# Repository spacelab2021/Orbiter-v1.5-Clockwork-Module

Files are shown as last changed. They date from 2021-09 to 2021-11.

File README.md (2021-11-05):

# Orbiter Clockwork Module
This Clockwork module allows the use of the Orbiter v1.5 Extruder in the Voron Afterburner.

## Features
One of the main issues I observed when using the orbiter was a lack of a quick filament release in additional to a lack of a suitable clockwork adapter that would swap an orbiter directly into the Afterburner ecosystem. Many of the issues observed were addressed with this Clockwork Module. This version provides a chain anchor for the Voron 2.4 and the Switchwire, a Cable Cover, and a quick filament release lever.

## Bill of Materials (BOM)

| Quantity | Name | Type |
|---|---|---|
| 1 | Orbiter v1.5 Extruder [Orbiter Thingiverse link](https://www.thingiverse.com/thing:4725897) | Hardware  |  
| 9 | M3 Heat Set Inserts [McMaster Link](https://www.mcmaster.com/94180A331) | Hardware  |  
| |94180A331 or suitable inserts (Thread Pitch 0.5, Installed Length 3.8mm, Diameter ~5mm) | | 
| 1 | M3x8mm SHCS | Hardware  |  
| 2 | M3x10mm SHCS | Hardware  |  
| 1 | M3x12 SHCS | Hardware  | 
| 2 | M3x20 SHCS | Hardware  |
| 1 | PTFE 50mm (Dragon) | Hardware  |
| 1 | Clockwork Adaptor - Front | Printable |
| 1 | Clockwork Adaptor - Back | Printable |
| 1 | Cable/Connector Cover | Printable |
| 1 | Filament Quick Release | Printable |
| 1 | Chain Anchor (Version for Voron 1.8/Trident/2.4 and Switchwire) | Printable |

## Assembly Guide
* [Orbiter Clockwork Assembly Guide](./docs/Orbiter_Clockwork_Manual.pdf)

## Orbiter Clockwork Module Images
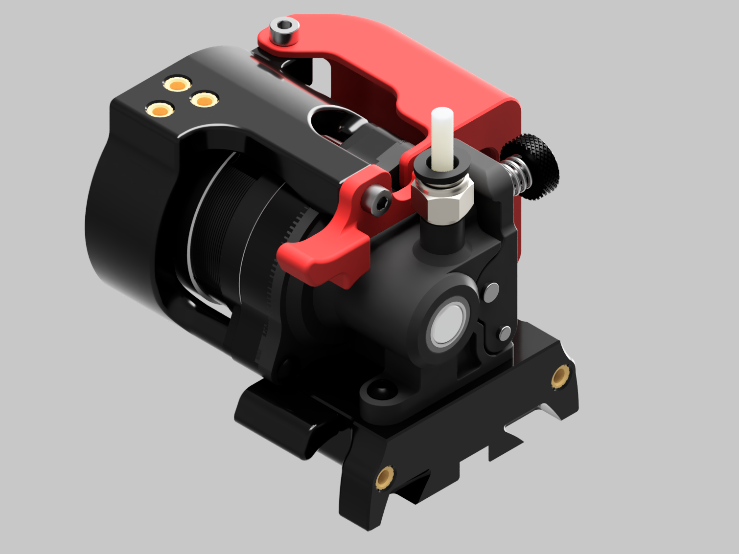
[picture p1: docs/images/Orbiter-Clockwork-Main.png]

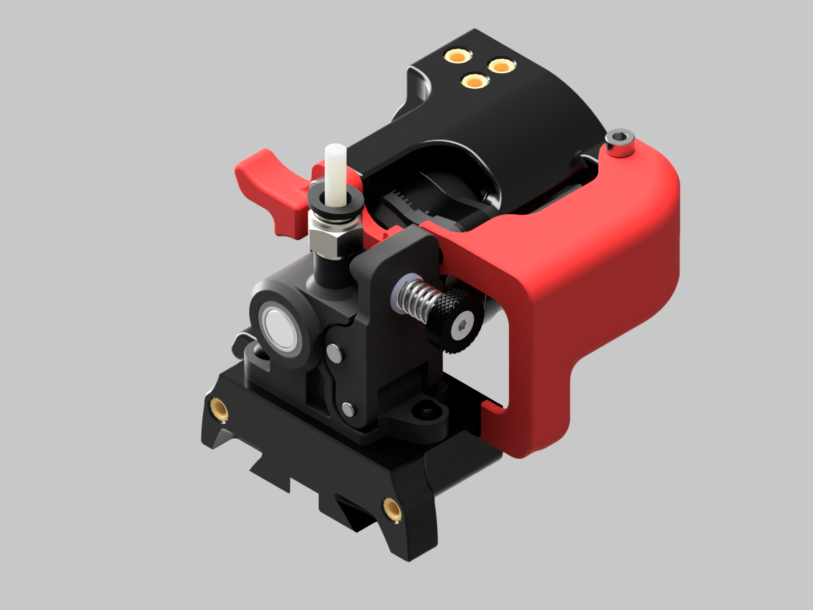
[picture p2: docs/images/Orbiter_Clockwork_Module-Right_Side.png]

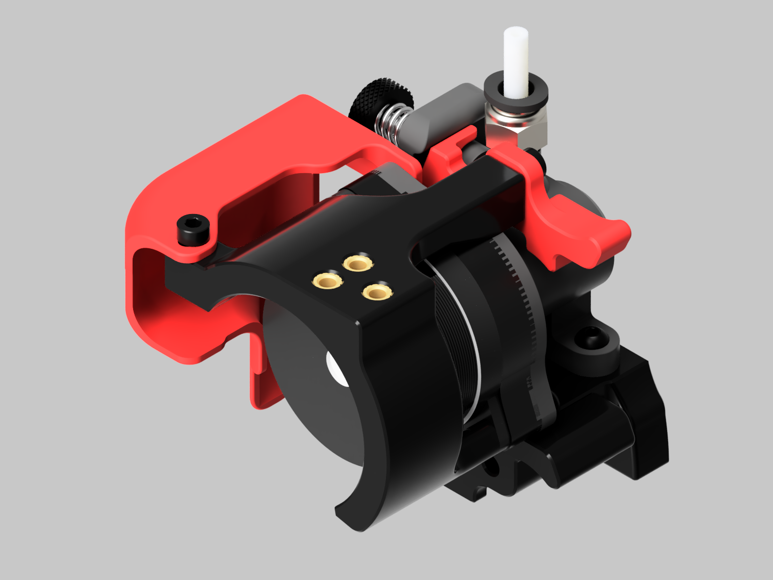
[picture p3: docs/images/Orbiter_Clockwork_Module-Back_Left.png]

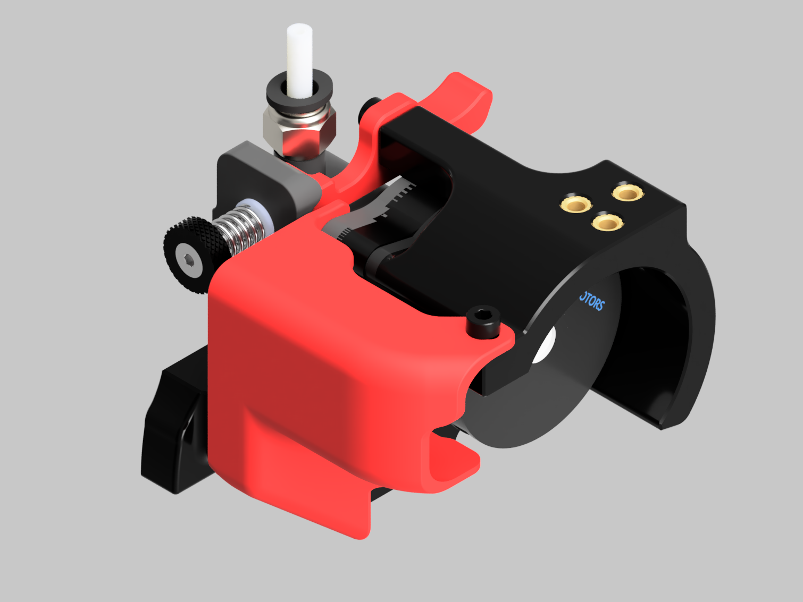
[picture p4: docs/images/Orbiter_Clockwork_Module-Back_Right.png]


## Release History
* Version 1.0 
   * Orbiter Clockwork Adaptor has been verified to fit and function on a Voron 2.4 and a Switchwire. Additional testing may be required to fix any minor or major issues that are identified in the future. If you observed any issues, please create an issue so it can be tracked.

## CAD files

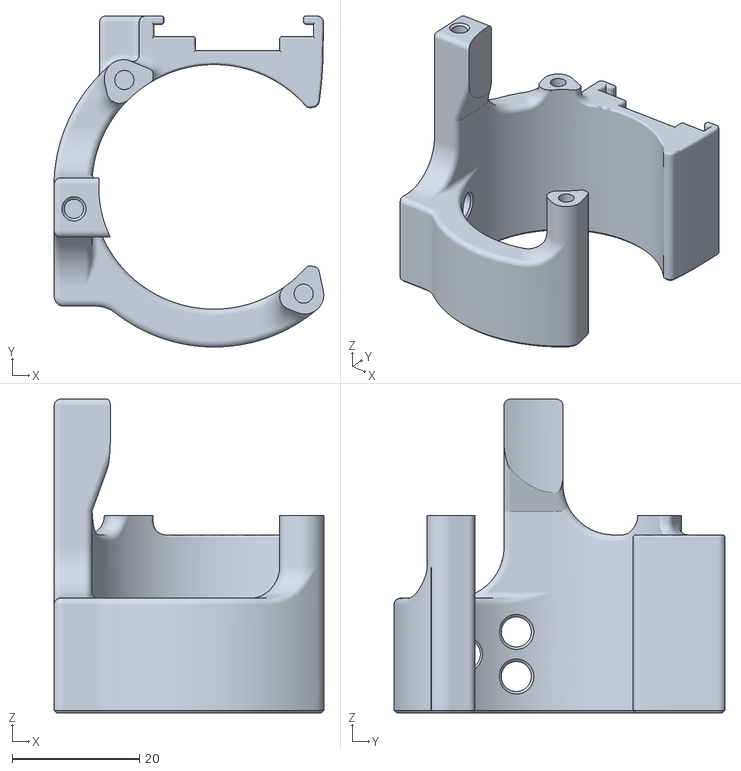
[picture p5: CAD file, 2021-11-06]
stl/Chain_Anchor-PCB_Mount-Generic-2.4.stl
42.3 x 52.0 x 49.2

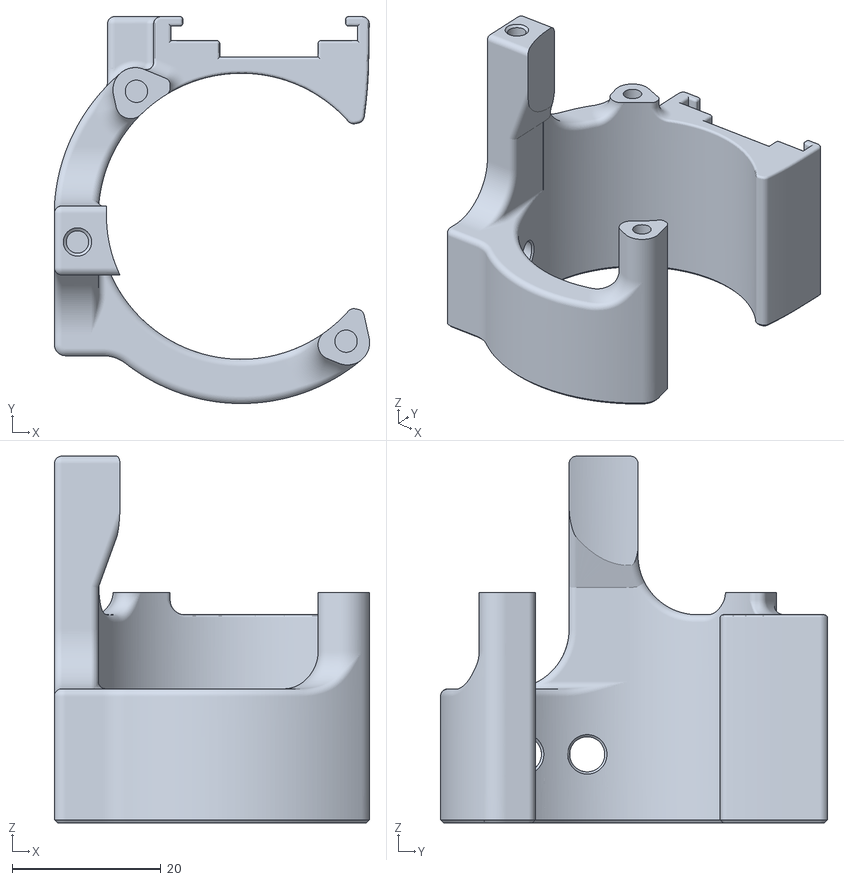
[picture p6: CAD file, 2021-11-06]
stl/Chain_Anchor-PCB_Mount-Igus-2.4.stl
42.3 x 52.0 x 49.2

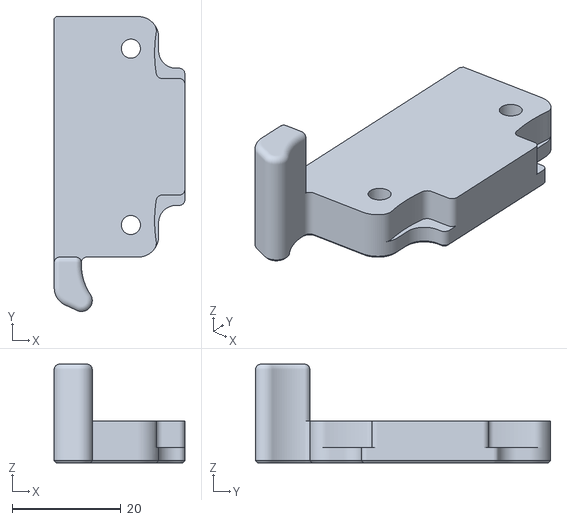
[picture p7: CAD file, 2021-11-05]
stl/Clockwork_Adaptor_Back.stl
24.0 x 54.2 x 18.1

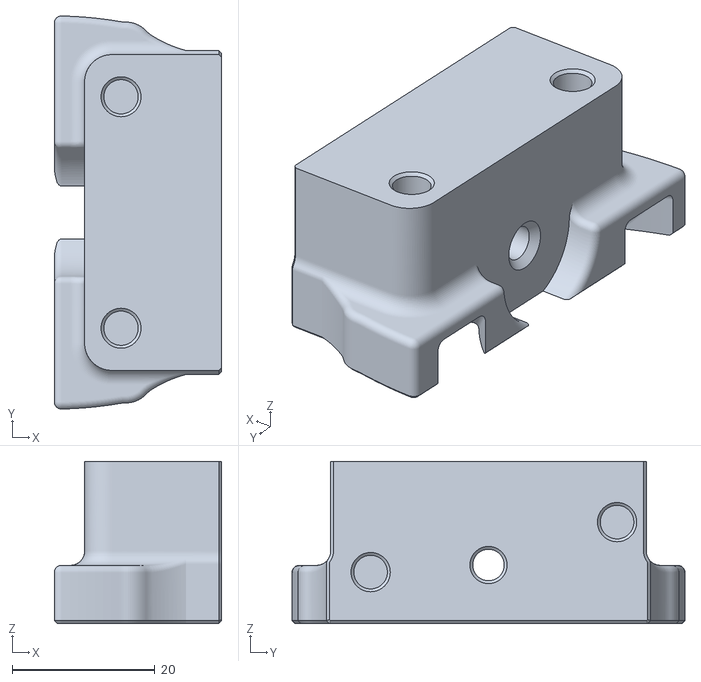
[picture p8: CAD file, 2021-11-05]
stl/Clockwork_Adaptor_Front.stl
23.4 x 55.0 x 22.7

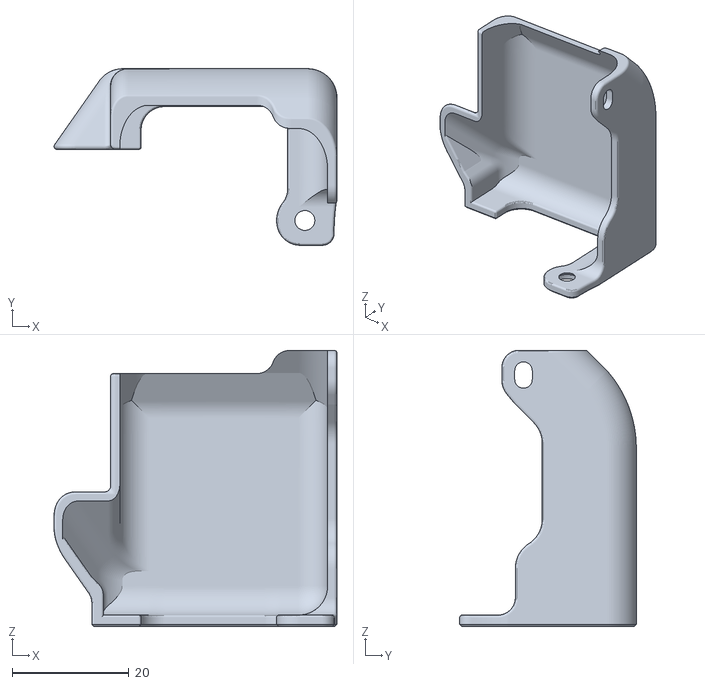
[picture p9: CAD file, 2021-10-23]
stl/[a]_PCB_Connector_Cover.stl
48.5 x 30.3 x 47.4

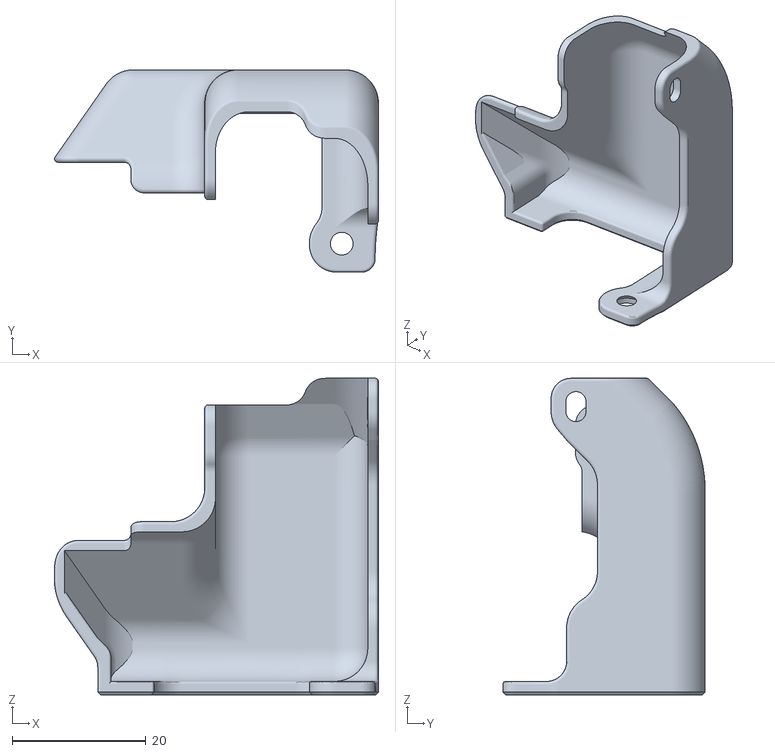
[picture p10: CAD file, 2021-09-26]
stl/[a]_Connector_Cover.stl
48.5 x 30.3 x 47.4

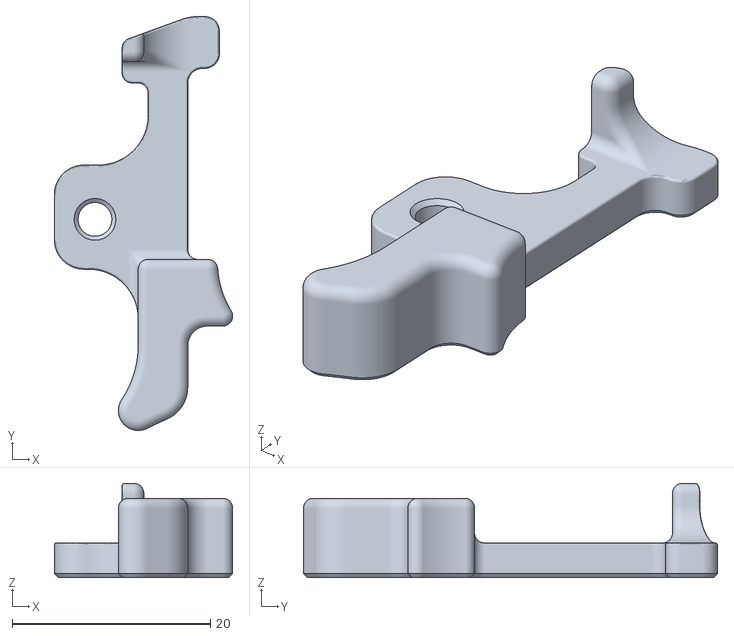
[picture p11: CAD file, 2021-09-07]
stl/[a]_Filament_release_lever.stl
18.0 x 41.7 x 9.50

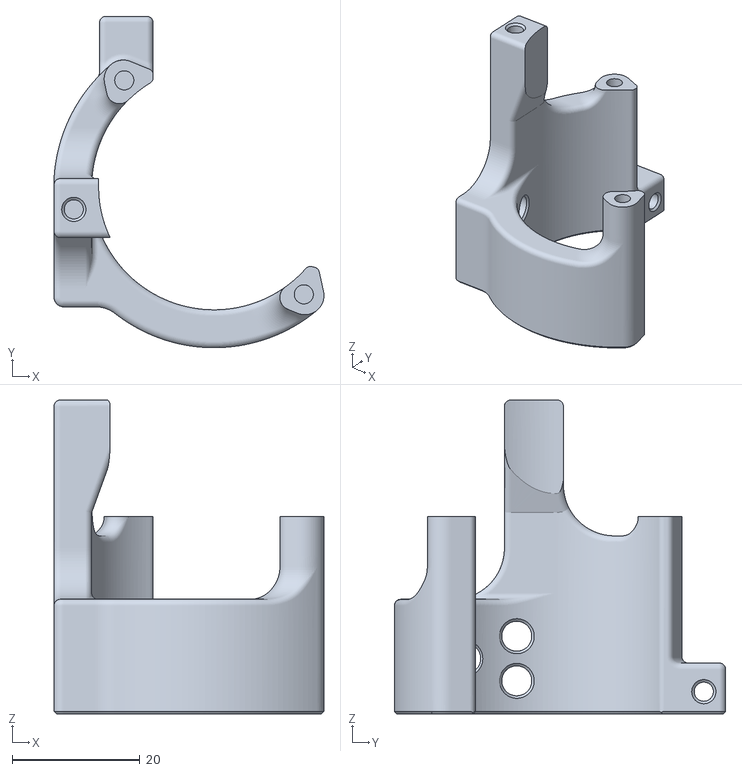
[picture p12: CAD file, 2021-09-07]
stl/Chain_Anchor-Voron_2.4.stl
42.3 x 52.0 x 49.2

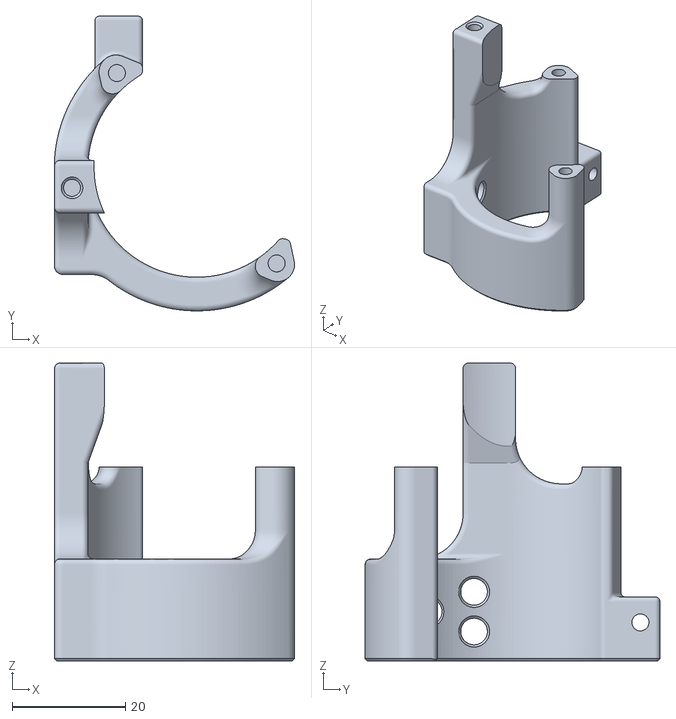
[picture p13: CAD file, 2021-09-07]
stl/Chain_Anchor_SwitchWire.stl
42.3 x 52.0 x 52.5

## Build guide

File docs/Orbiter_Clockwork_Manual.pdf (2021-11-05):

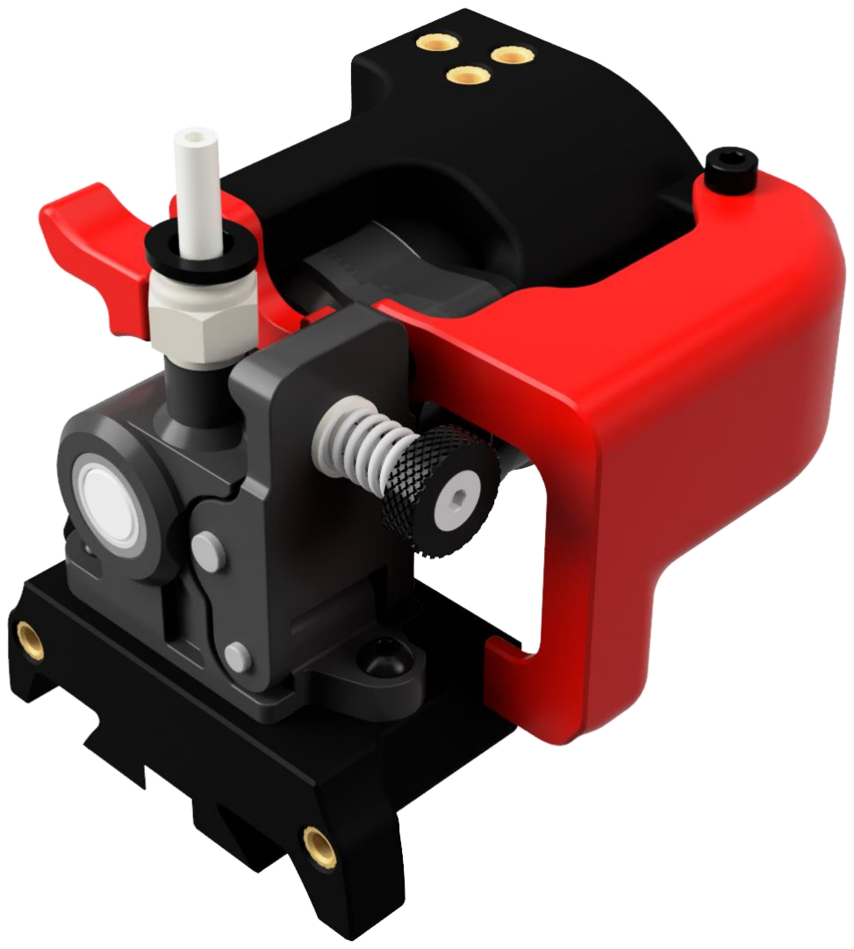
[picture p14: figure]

# ORBITER CLOCKWORK ASSEMBLY MANUAL

## MANUAL VERSION 1.0.3

Orbiter Clockwork Assembly Manual | 2

## HARDWARE

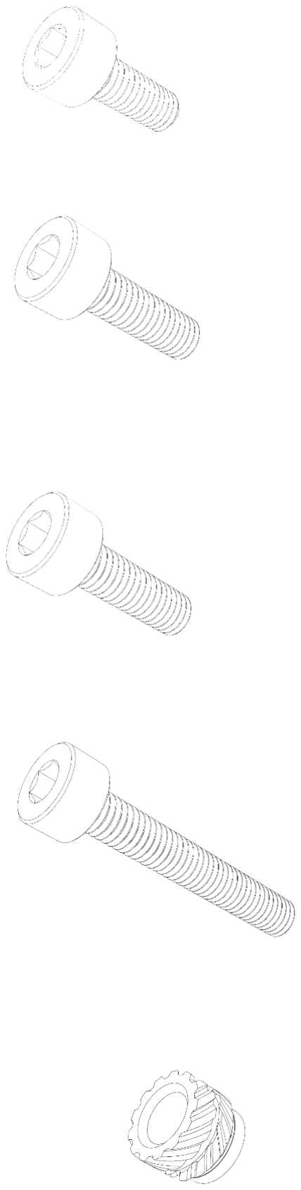
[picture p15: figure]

### SOCKET HEAD CAP SCREW (SHCS)

Metricfastenerwithacylindricalheadand hex drive.

### M3x8 Quantity 1

### SOCKET HEAD CAP SCREW (SHCS)

Metric fastener with a cylindrical head and hex drive.

### M3x10 Quantity 2

### SOCKET HEAD CAP SCREW (SHCS)

Metric fastener with a cylindrical head and hex drive.

### M3x12 Quantity 1

### SOCKET HEAD CAP SCREW (SHCS)

Metric fastener with a cylindrical head and hex drive.

### M3x20 Quantity 2

### TAPERED HEAT-SET INSERTS FOR PLASTIC

### The tapered shape makes it easier to guide these inserts into a hole during installation. Use a drill bit to create a straight hole, then taper the top half. Heat inserts with a

soldering tip so that they melt the plastic when installed.

### As the plastic cools, it solidifies around the knurls and ridges on the insert for excellent resistance to both torque

and pull-out.

### M3 Brass Heat-Set Insert Quantity: 9

### PTFE Tube

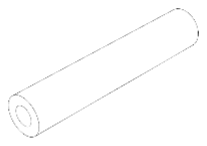
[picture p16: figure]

### The PTFE tube is used between the Orbiter extruder and the Toolhead. Specific hot end lengths are listed below:

### Phaetus Dragon Hotend PTFE Tube Length 50mm

### E3D V6 Hot end PTFE Tube Length ??mm (Not Tested Yet)

### Slice Engineering Mosquito Hot end PTFE Tube Length ??mm (Not Tested Yet)

## PRINTED PARTS

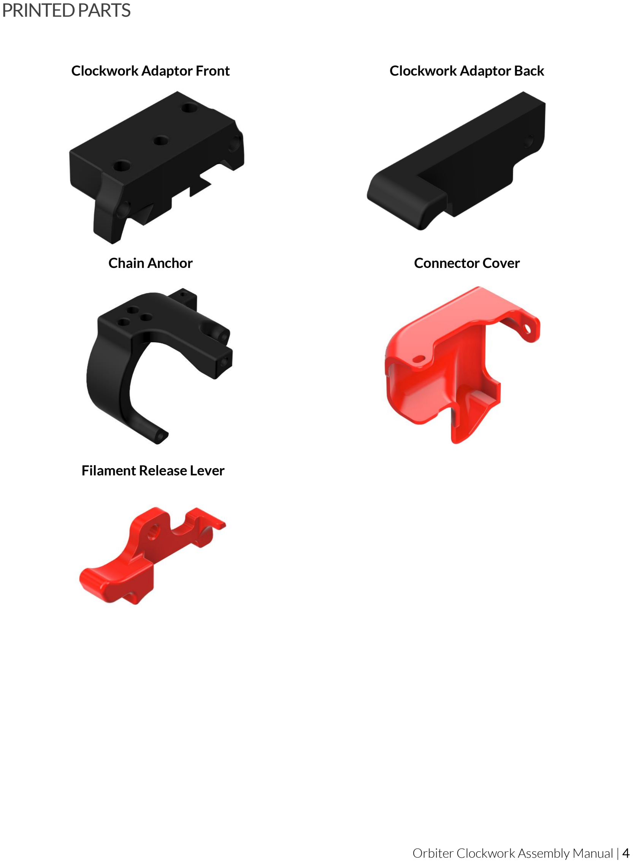
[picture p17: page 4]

Clockwork Adaptor Front | Clockwork Adaptor Back

### Chain Anchor

### Connector Cover

### Filament Release Lever

## ASSEMBLYGUIDE

# Assembly A. Heat-Set Inserts

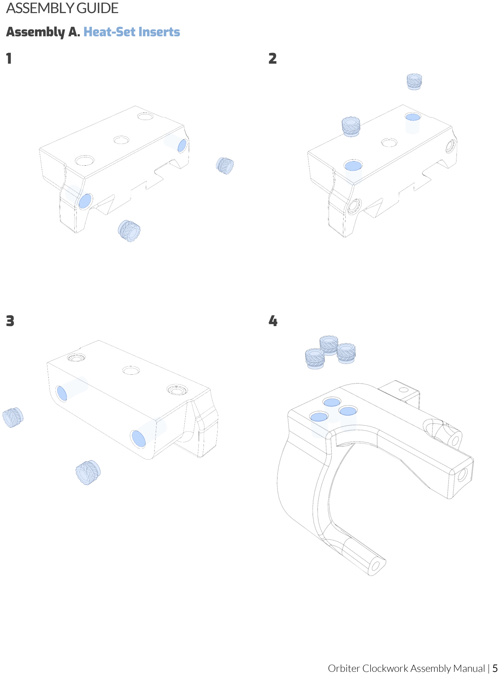
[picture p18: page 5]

1 2

3 4

# Assembly B. Orbiter Clockwork Adapter

5

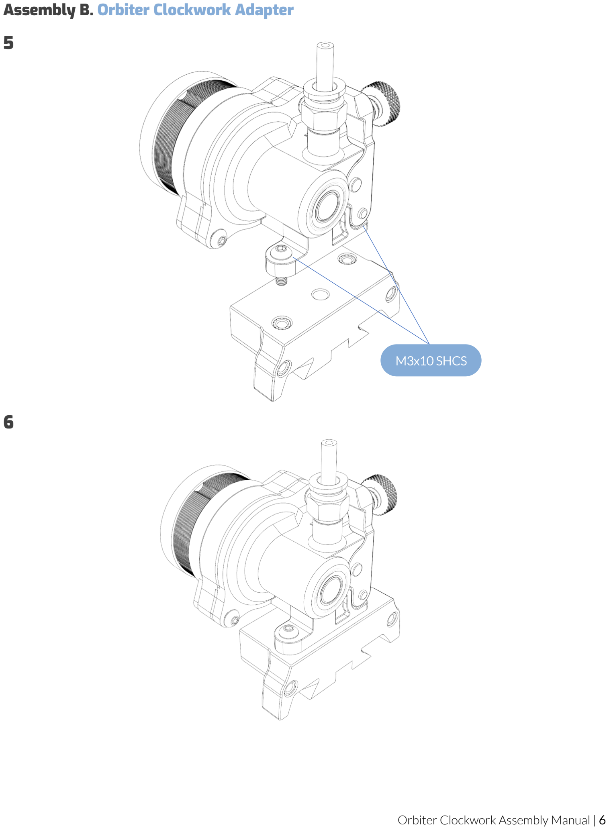
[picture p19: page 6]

6

M3x10 SHCS

# Assembly C. Connecter Cover and Chain Anchor

7 8

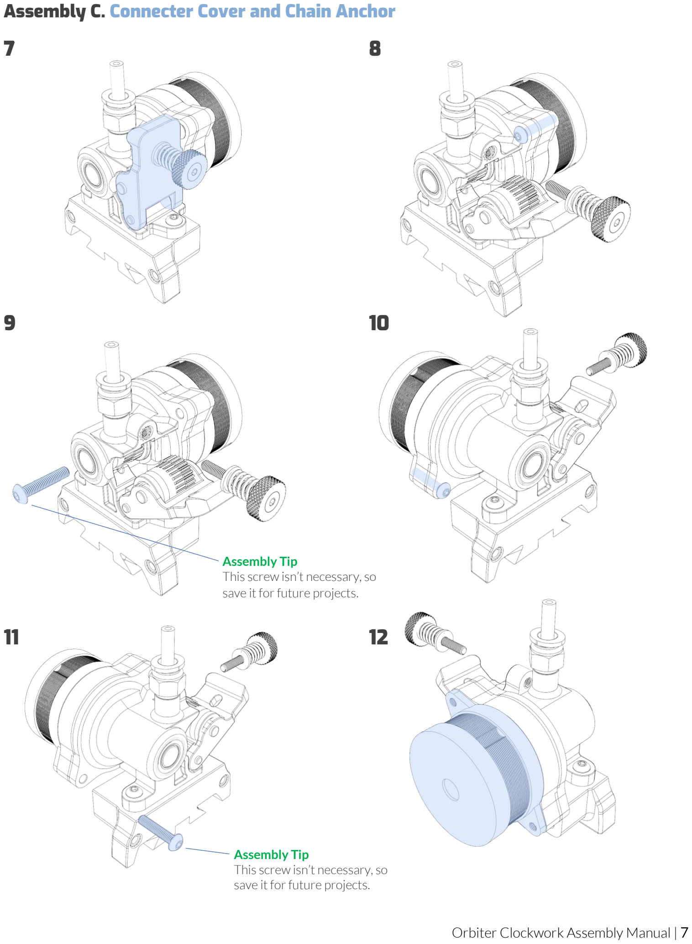
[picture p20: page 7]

9 10

11 12

Assembly Tip
This screw isn’t necessary, so save it for future projects.

Assembly Tip
This screw isn’t necessary, so save it for future projects.

13 14

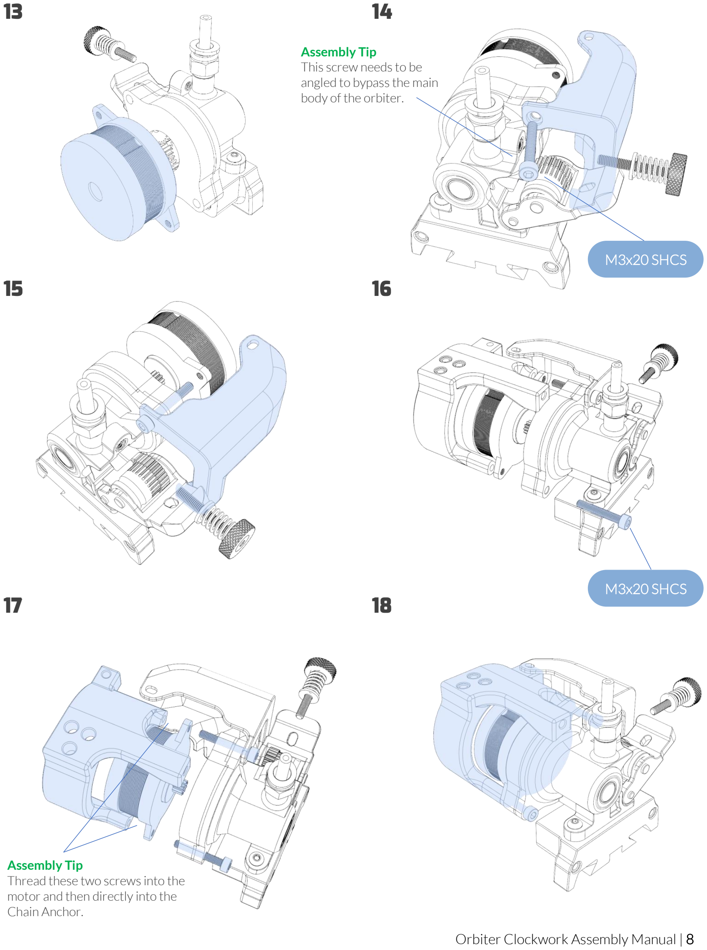
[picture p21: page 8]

15 16

17 18

M3x20 SHCS

M3x20 SHCS

Assembly Tip
Thread these two screws into the motor and then directly into the Chain Anchor.

Assembly Tip
This screw needs to be
angled to bypass the main
body of the orbiter.

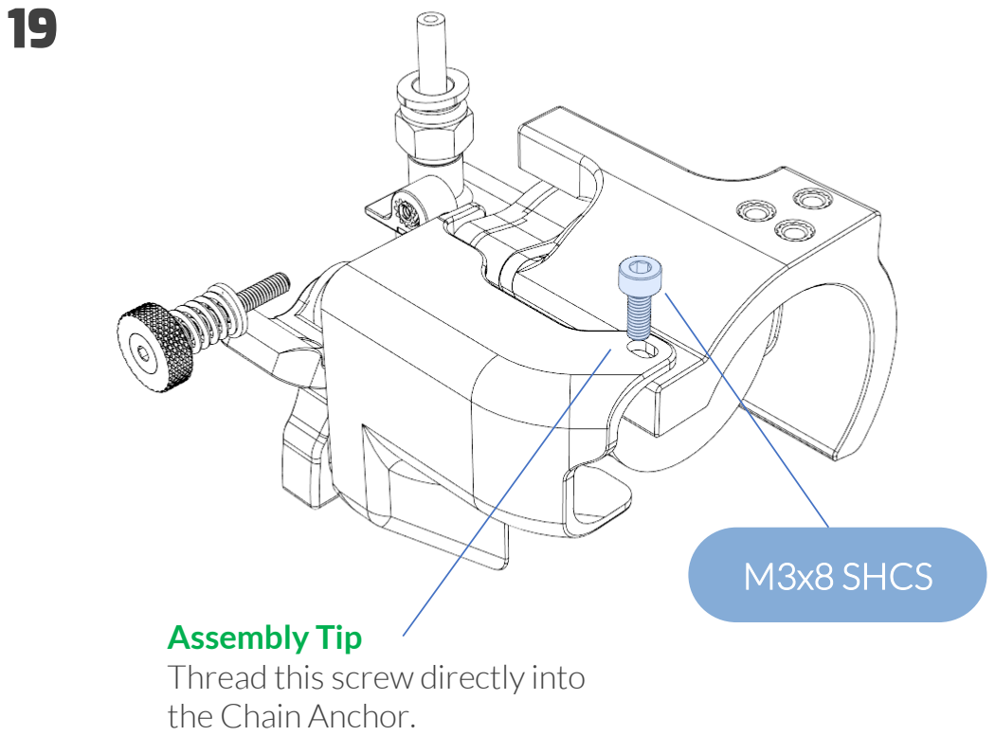
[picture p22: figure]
M3x8 SHCS; Assembly Tip Thread this screw directly into the Chain Anchor.

# Assembly D. Filament Quick Release Lever

20 21

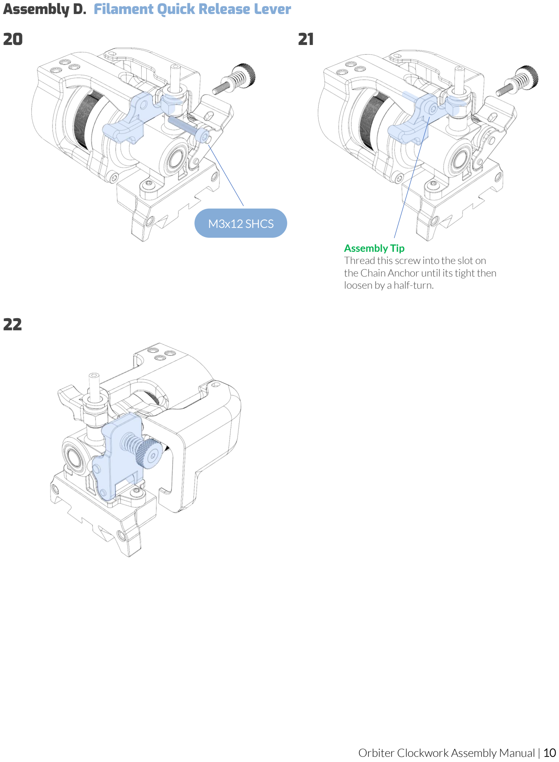
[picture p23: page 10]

22

Assembly Tip
Thread this screw into the slot on the Chain Anchor until its tight then loosen by a half-turn.

M3x12 SHCS

# Assembly E. Final Assembly

23

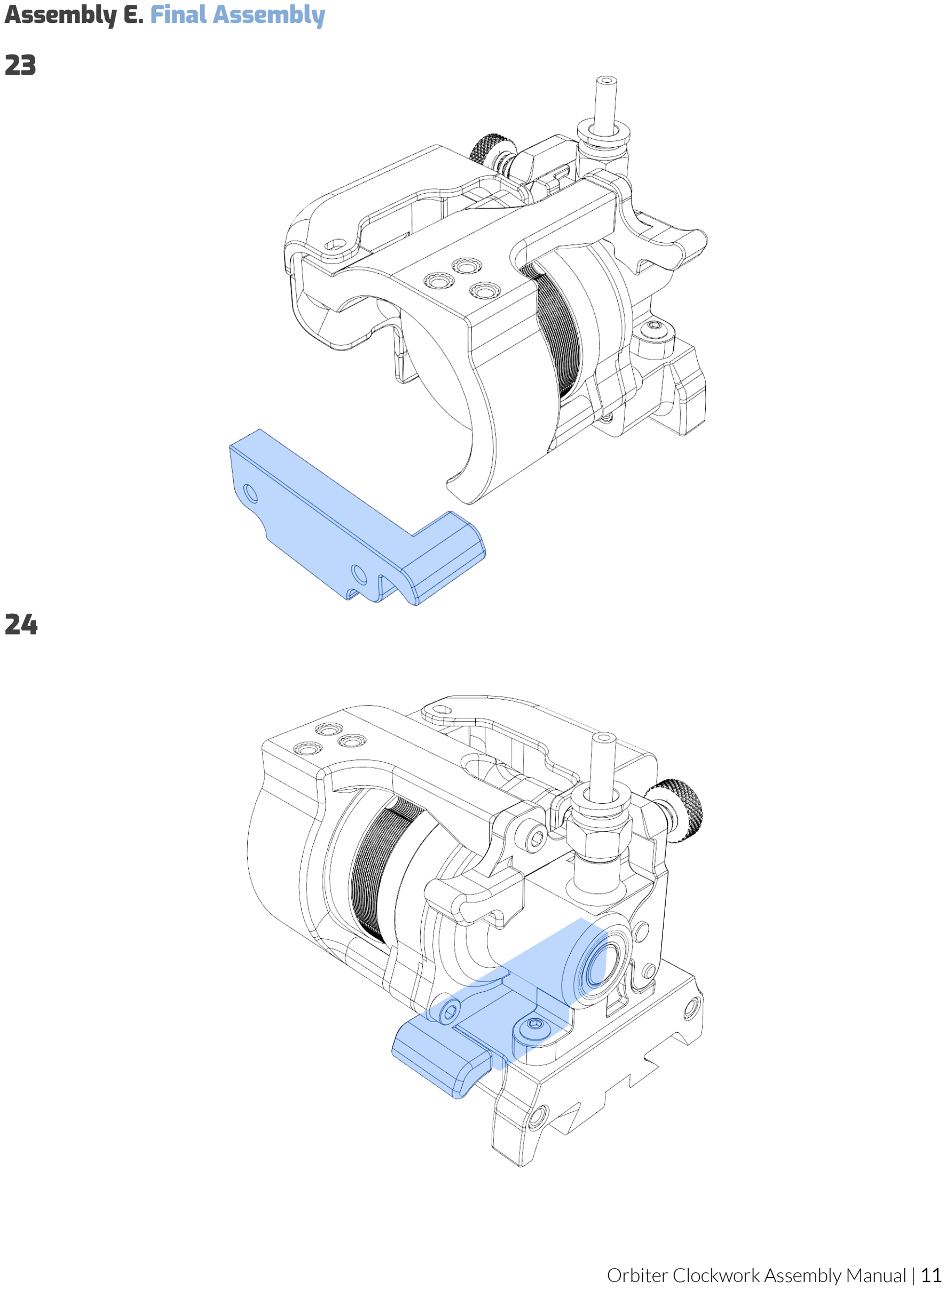
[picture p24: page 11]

24

25

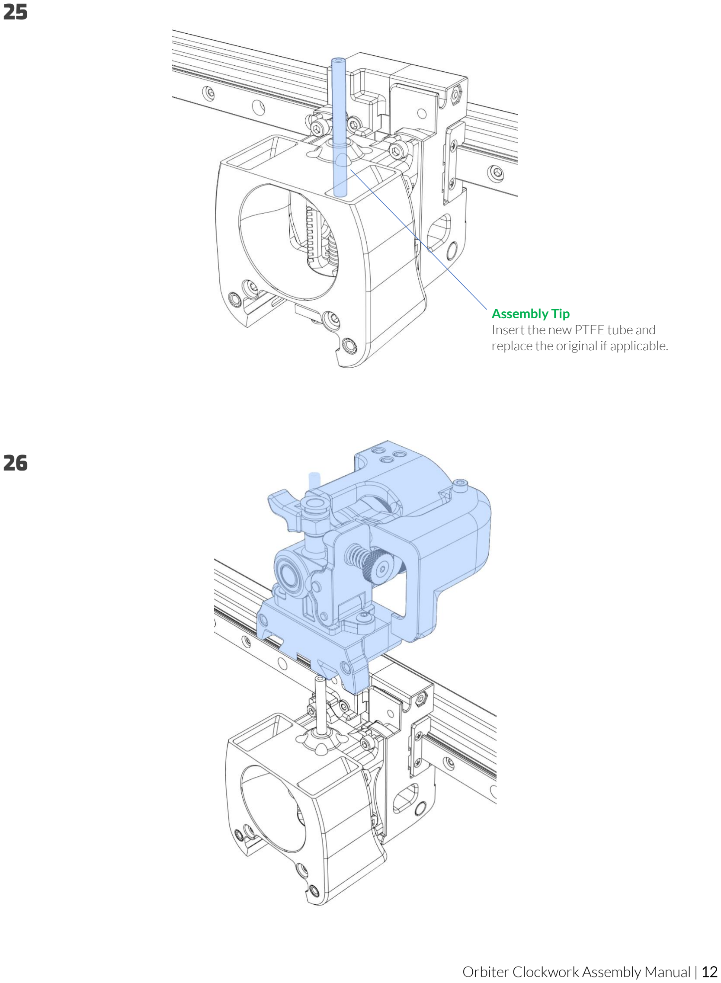
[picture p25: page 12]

26

Assembly Tip
Insert the new PTFE tube and replace the original if applicable.

27

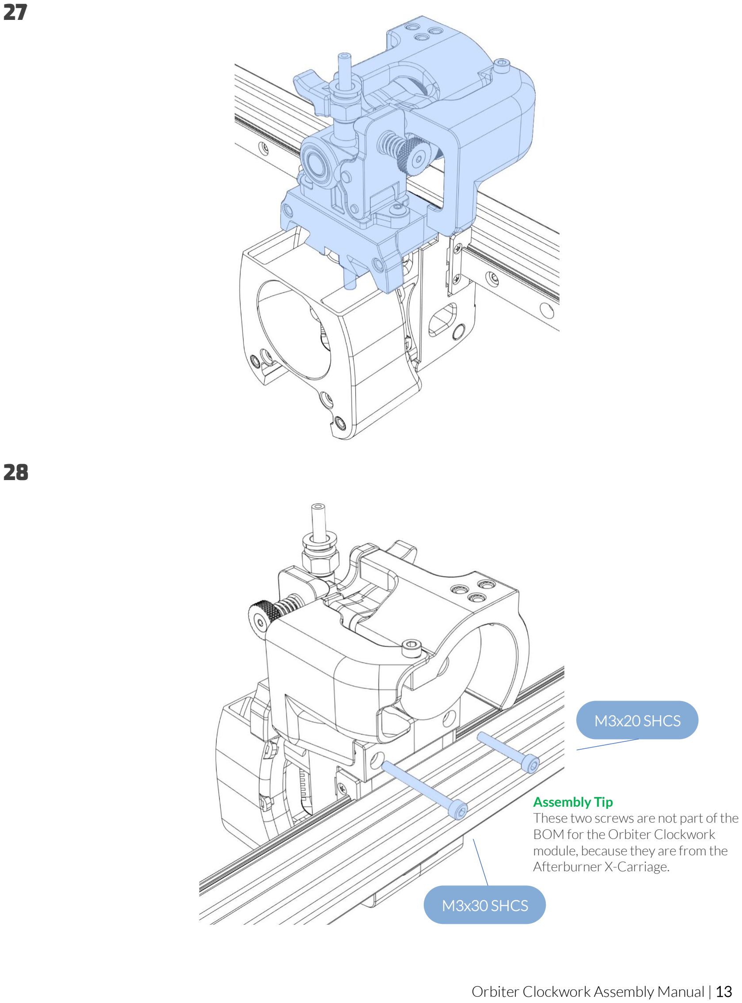
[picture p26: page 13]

28

M3x20 SHCS

M3x30 SHCS

Assembly Tip
These two screws are not part of the BOM for the Orbiter Clockwork module, because they are from the Afterburner X-Carriage.

29

30

M3x30 SHCS

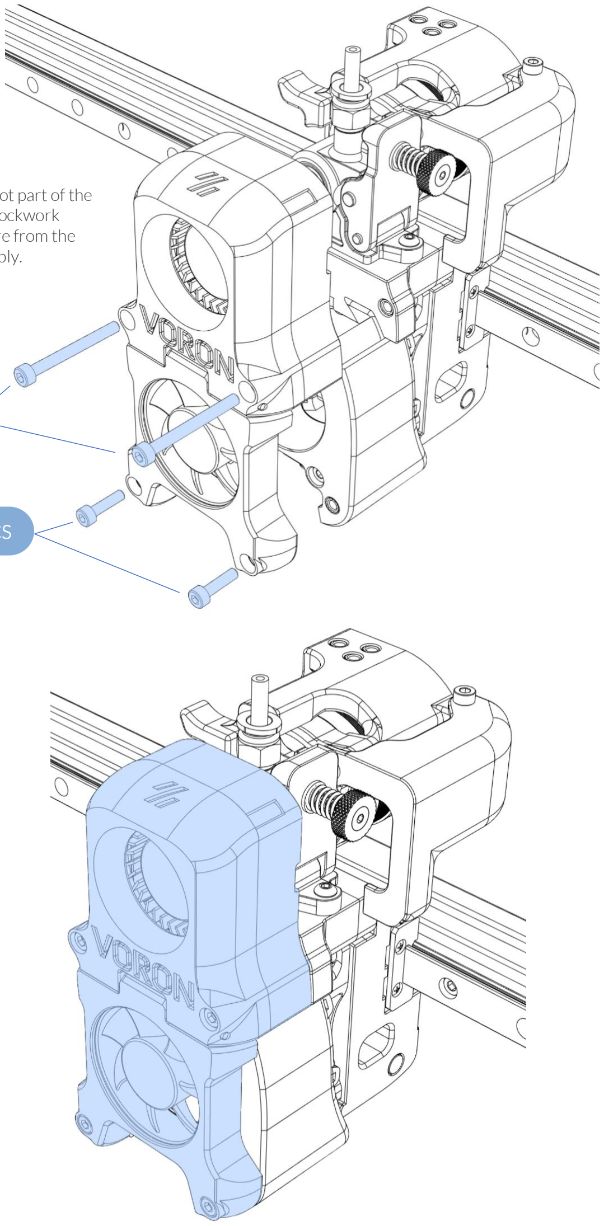
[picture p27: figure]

M3x12 SHCS

Assembly Tip
These four screws are not part of the BOM for the Orbiter Clockwork module, because they are from the Afterburner Fan Assembly.

# Assembly Complete

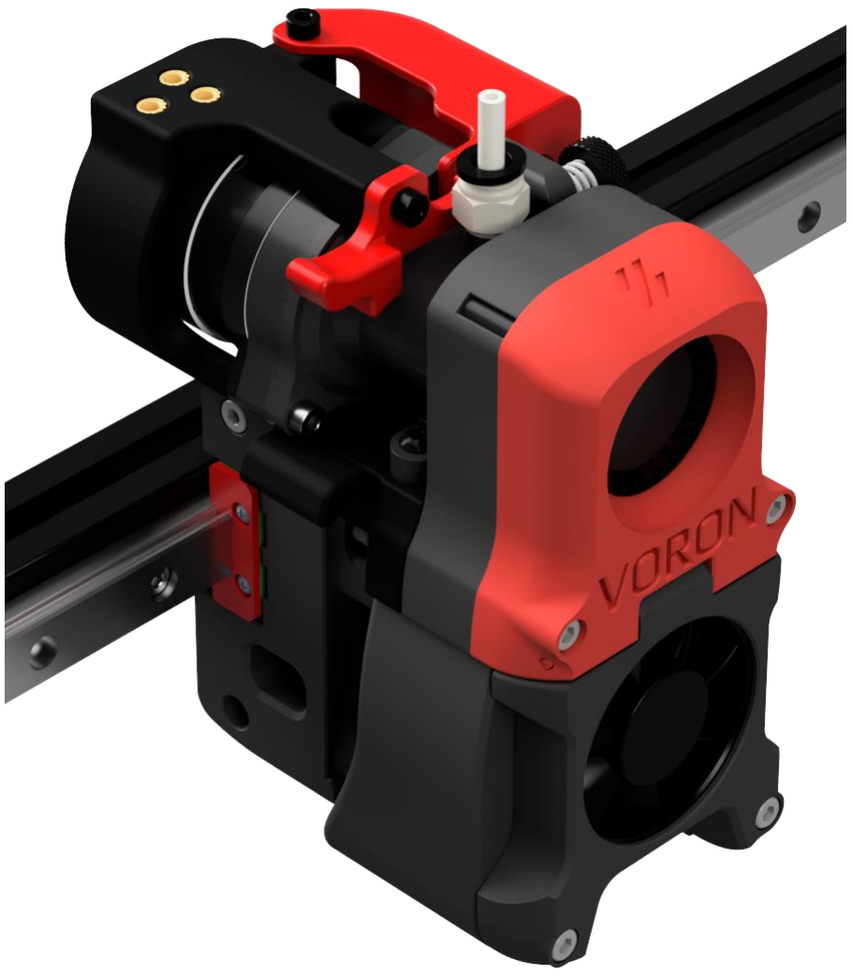
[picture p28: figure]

# Next Steps

## NEXT STEP: SETUP & CALIBRATION

This manual was designed to be a simple reference manual for the assembly process.
For further details on the setup of the electronics and other initial steps of your new printer please visit the VORON documentation available on github and docs.vorondesign.com.

## HOW TO GET HELP

If you need assistance with your build, we’re here to help. Head on over to the VORON Discord group and post your questions. This is the primary medium to help VORON Users and we have a great community that can help you out if you get stuck.

## ADDITIONAL RESOURCES

https://github.com/VoronDesign/https://github.com/spacelab2021/Orbiter-Clockwork-Module

Get the Latest Version of this document: https://github.com/spacelab2021/Orbiter-Clockwork-Module/blob/main/docs/Orbiter_Cockwork_Manual.pdf

## https://discord.gg/voron

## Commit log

2021-09-07 Initial Upload of stl files.
    [Chain Anchor - Compressed - SwitchWire.stl, Chain Anchor - Compressed - Voron 2.4.stl, Clockwork Adaptor - Back.stl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]
2021-09-07 Updated Organization Structure
    [Chain Anchor - Compressed - SwitchWire.stl, Chain Anchor - Compressed - Voron 2.4.stl, Clockwork Adaptor - Back.stl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]
2021-09-08 Added Manual and renamed stl files.
    [Chain_Anchor-Voron_2.4.stl, Chain_Anchor_SwitchWire.stl, Clockwork_Adaptor_Back.stl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]
2021-09-08 Added additional screw lengths to BOM.
2021-09-08 Updated Step file with correct screw lengths
2021-09-09 Updated BOM
2021-09-13 Fixed unreadable assembly tip font
2021-09-13 Created BOM Table
2021-09-26 Updated the name and file
    [[a]_Connector_Cover.stl, [a]_Wire_Cover.stl]
2021-10-22 Added m3x10 screw to the BOM
2021-10-22 Changed heat-set insert size on mount
    [Clockwork_Adaptor_Front.stl]
2021-10-23 PCB Update
    Added the modified PCB Connector Cover which included the updated STL and Step files.
    [[a]_PCB_Connector_Cover.stl]
2021-10-24 Updated STEP file with PCB cover.
2021-10-27 Updated the BOM
    Removed the m3x16 screw as it's no longer needed and is depreciated. It's been replaced with a m3x12.
2021-11-04 Added the PCB Chain Anchor
    [Chain_Anchor-PCB_Mount-Generic-2.4.stl, Chain_Anchor-PCB_Mount-Igus-2.4.stl.stl]
2021-11-05 Increased the height
    The old mounts were hitting the chain on the left side when it engaged with the x-y gantry. This update increases the height by 5mm.
    [Clockwork_Adaptor_Back.stl, Clockwork_Adaptor_Front.stl]
2021-11-05 Updated BOM
    The afterburner mount was updated to clear the cable chain, and the ptfe tube needs to be 5mm higher.
2021-11-05 Updated BOM in manual
    Updated the ptfe tube length.
2021-11-05 Updated Afterburner mount.
    Height was increased by 5mm to clear the cable chain.
2021-11-06 Revised Chain Anchor for PCB.
    [Chain_Anchor-PCB_Mount-Generic-2.4.stl, Chain_Anchor-PCB_Mount-Igus-2.4.stl, Chain_Anchor-PCB_Mount-Igus-2.4.stl.stl]
2021-11-06 Revised Generic Chain Anchor for PCB
    [Chain_Anchor-PCB_Mount-Generic-2.4.stl]
